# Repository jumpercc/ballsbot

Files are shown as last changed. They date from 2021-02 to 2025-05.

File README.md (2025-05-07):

# Miniature self driving car

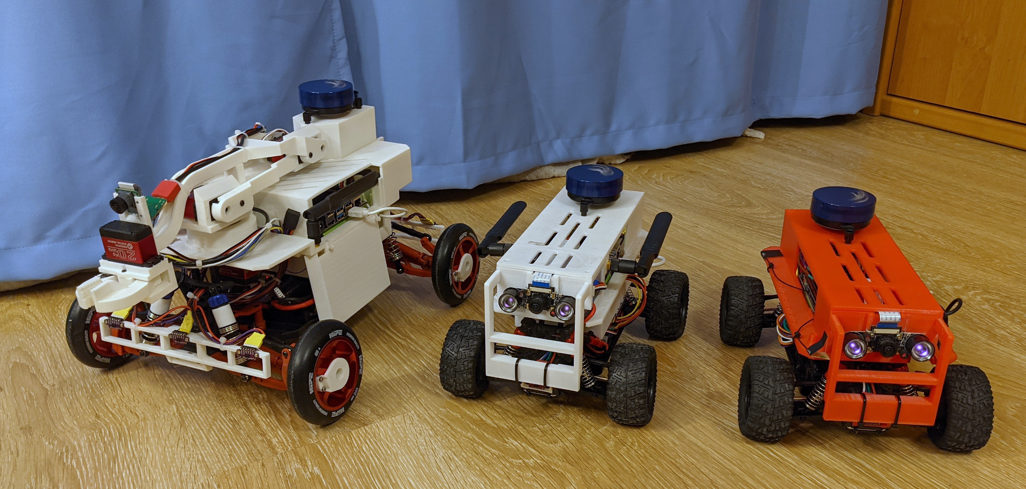
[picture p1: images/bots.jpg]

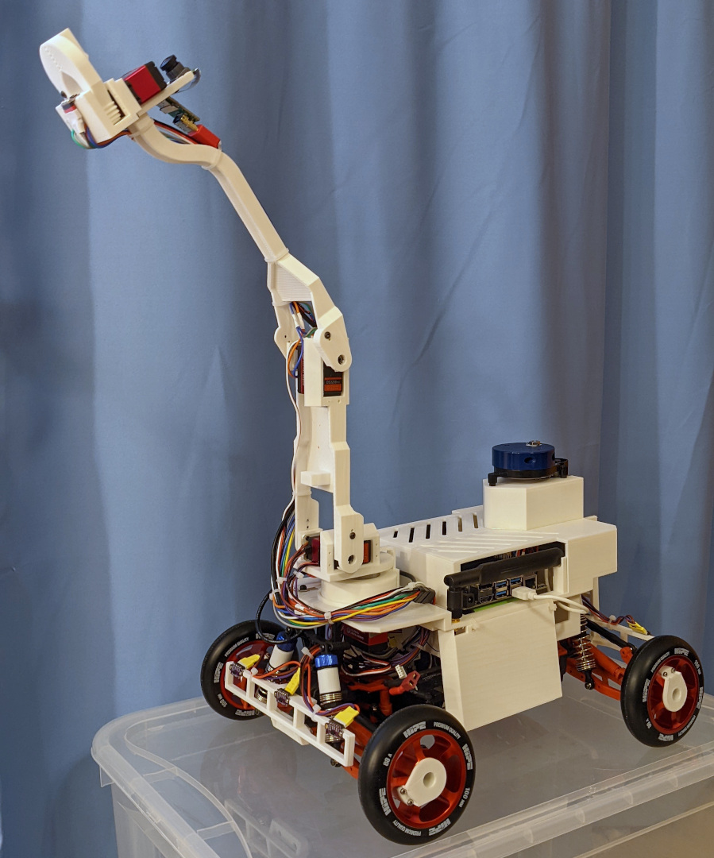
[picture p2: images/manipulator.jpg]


[A video how to construct this car](https://www.youtube.com/watch?v=rkNG0EHzA00&list=PLYvKlIOUsVXJjlYiZFUibLezPqPUq2qsj&index=1) (russian, 1/16 (small) version)

[Android app for teleoperation](https://github.com/jumpercc/ballsbot-teleoperation-android)

## Requirements

### Hardware: common for 1/16 and 1/10 models

- Nvidia Jetson Nano Developer Kit [aliexpress](https://www.aliexpress.com/item/4000765500472.html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)
- 64 GB micro sd card
- inner (not usb!) wi-fi card like [that one](https://www.aliexpress.com/item/4000144144831.html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) and IPEX Connector antennas for it
- T208 (1/16 preferred, 1/10 required) or T200 18650 UPS HAT Shield for NVIDIA Jetson Nano Developer Kit [aliexpress](https://www.aliexpress.com/item/4001332826343.html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,searchweb201602_,searchweb201603_)
- 6 (for T208) or 4 (for T200) 18650 Lithium Rechargeable Battery [aliexpress](https://www.aliexpress.com/item/32807032859.html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)
- YDLIDAR X2L or similar [aliexpress](https://www.aliexpress.com/item/4000018415971.html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)
- 9-DOF IMU BNO055 [aliexpress](https://www.aliexpress.com/item/32805406886.html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)
- PCA9685 16 Channel 12-bit PWM Servo motor Driver I2C [aliexpress](https://www.aliexpress.com/item/4000468996665.html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)
- short USB - USB-C data cable like [this one](https://www.aliexpress.com/item/32771873030.html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)
- access to 3D printer
- cables, screws, etc
- tools

### Hardware: 1/16 specific

- Remo Hobby Smax 1:16 RH1635
- SURPASS HOBBY KK 35A ESC Waterproof Electric Speed Controller for 1/16 RC Car Brushless Motor Power system [aliexpress](https://www.aliexpress.com/item/4000004474965.html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)
- Two KY-003 hall sensor module for Arduino [aliexpress](https://www.aliexpress.com/item/32907115789.html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)
- neodymium magnet about 20x3x2 mm size
- IMX219 Camera 8MP Infrared Night Vision 160 Degree FOV + 2 Infrared LED Lights [aliexpress](https://www.aliexpress.com/item/4000215557127.html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)
- 4 Channel IIC I2C Logic Level Converter Bi-Directional Module 5V to 3.3V [aliexpress](https://www.aliexpress.com/item/32771873030.html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)
- two laser distance sensors VL53L0X (6 pin) [aliexpress](https://www.aliexpress.com/item/32842745623.html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)
- additional camera, servos and others for manipulator

### Hardware: 1/10 with manipulator specific

- Remo Hobby Mmax 1:10 RH1035
- 2x Raspberry Pi Camera V2 [aliexpress](https://www.aliexpress.com/item/32846859601.html?spm=a2g0s.9042311.0.0.27424c4dI1W4Uq)
- 2x IMX219 camera sensors [aliexpress](https://www.aliexpress.com/item/4000273558224.html?spm=a2g0s.9042311.0.0.27424c4dI1W4Uq)
- 2x longer CSI cables
- engine (preferred) [aliexpress](https://www.aliexpress.com/item/4000957170077.html?spm=a2g0s.9042311.0.0.27424c4dI1W4Uq)
  - HobbyWing QuicRun 3650 Sensored Brushless G2 (25.5T)
  - QuicRun 10BL60
  - programming card
  - 3s accumulator (like Sunpadow Li-Po 3S1P 5200mAh) [market](https://market.yandex.ru/search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)
- 5x strong servos (I have 3x 30kg and 2x 20kg) [aliexpress](https://www.aliexpress.com/item/1943129663.html?spm=a2g0s.9042311.0.0.27424c4dI1W4Uq)
- 4x AS5600 magnetic encoders [aliexpress](https://www.aliexpress.com/item/4000507199893.html?spm=a2g0s.9042311.0.0.27424c4dI1W4Uq)
- 4x scooter wheels (like HIPE 5spoke 100 mm) [market](https://market.yandex.ru/catalog--aksessuary-i-zapchasti/18071952/list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)
- 1 meter thin hdmi cable
- Arducam CSI to HDMI Cable Extension Module (pack of 2) [arducam](https://www.arducam.com/product/arducam-csi-hdmi-cable-extension-module-15pin-60mm-fpc-cable-raspberry-pi-camera-specific-pack-2-1-set/)
- LTE, GPS (FIXME: haven't tested yet)
  - HUAWEI ME906e with antennas [aliexpress](https://www.aliexpress.com/item/1850815686.html?spm=a2g0s.9042311.0.0.27424c4dI1W4Uq)
  - NGFF M.2 Key B to USB 3.0 Adapter Expansion Card [aliexpress](https://www.aliexpress.com/item/4001209010055.html?spm=a2g0s.9042311.0.0.27424c4dI1W4Uq)
  - usb cable [aliexpress](https://www.aliexpress.com/item/4001289900478.html?spm=a2g0s.9042311.0.0.27424c4dI1W4Uq)
- 7x laser distance sensors VL53L0X [aliexpress](https://www.aliexpress.com/item/32842745623.html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)
- TCA9548 I2C 8-way multi-channel Expansion Board [aliexpress](https://www.aliexpress.com/item/4000067621113.html?spm=a2g0s.9042311.0.0.27424c4dPYaIDF)

### Software

- JetPack 4.6 [configuration steps](./configuration.txt)
- code from this repo
- ROS
- [Jupyter](https://jupyter.org/install) (```pip3 install notebook```)
- [YDLidar-ros](https://github.com/YDLIDAR/ydlidar_ros) for lidar (use [pdf](https://www.ydlidar.com/Public/upload/files/2020-04-13/YDLIDAR-X2-USER%20Manual.pdf) too) and install tf ros package
- ```pip3 install adafruit-pca9685``` for PCA9685
- [RTIMULib](https://github.com/jetsonhacks/RTIMULib/tree/master/Linux/python) for IMU and you need this fix (for i2c bus 0, except AS5600 magnetic encoder via TCA9548):
```
$ git diff
diff --git a/RTIMULib/RTIMUSettings.cpp b/RTIMULib/RTIMUSettings.cpp
index 783dbff..9c0333e 100644
--- a/RTIMULib/RTIMUSettings.cpp
+++ b/RTIMULib/RTIMUSettings.cpp
@@ -470,7 +470,7 @@ void RTIMUSettings::setDefaults()
     m_imuType = RTIMU_TYPE_AUTODISCOVER;
     m_I2CSlaveAddress = 0;
     m_busIsI2C = true;
-    m_I2CBus = 1;
+    m_I2CBus = 0;
     m_SPIBus = 0;
     m_SPISelect = 0;
     m_SPISpeed = 500000;
```

### SD card image

You can download SD card images from [here](https://disk.yandex.ru/d/XgYrkfBPJS2h5Q?w=1).
Install bare JetPack 4.6 first to upgrade jetson firmware.
Images are for 64GB SD cards.
```gunzip -c ballsbot-sd-2021-02-11.tgz | sudo dd of=/dev/sdb```

Login& password: `ballsbot`.

You need to connect to your wi-fi and make this connection "avaliable for all users" (checkbox in network settings).

### Dev docker

```
docker build -t ballsbot -f docker/Dockerfile .
docker run -d -v `pwd`:/home/ballsbot/projects/ballsbot -p 127.0.0.1:8080:8080 ballsbot
docker exec -it HASH-HERE bash

rm /home/ballsbot/catkin_ws/src/ballsbot_detection
source /opt/ros/melodic/setup.bash && cd /home/ballsbot/catkin_ws/ && catkin_make && source devel/setup.bash

apt-get update
/home/ballsbot/projects/ballsbot/scripts/make-ros-modules.sh  # ok if fails due to invalid arch

/home/ballsbot/projects/ballsbot/scripts/run-jupyter.sh --allow-root --port=8080 --ip=`ifconfig | grep -F 'inet ' | grep -vF 127.0.0.1 | awk '{print $2}'`
```

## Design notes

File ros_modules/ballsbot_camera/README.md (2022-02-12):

# Детектор объектов в камере, модуль для ROS

- берёт данные с камеры (csi, gstreamer)
- распознаёт объекты через SSD MobileNet
- публикует результаты

Ввиду нетривиальности сборки TensorRT кода, собрал его в отдельную библиотеку и положил рядом.
Вот исходники для [libuffssd.so](https://github.com/jumpercc/TensorRT/blob/release/8.0-jetson-nano-crosscompile-ssd/samples/sampleUffSSD/sampleUffSSD.cpp)

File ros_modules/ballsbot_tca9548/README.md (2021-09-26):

# ROS модуль для TCA9548

Переключатеть между группами из i2c устройств.

Можно читать данные с датчиков, i2c адреса которых конфликтуют.

Поддерживается до восьми устройств с одним адресом на одной TCA9548.

А, ввиду возможности задания адреса самой TCA9548, до 64ёх на одной i2c шине (через 8 TCA9548).

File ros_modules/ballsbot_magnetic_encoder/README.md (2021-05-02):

# Jetson I2C driver for rotary magnetic encoder (ROS node)

Inspired by [Arduino library](https://github.com/sosandroid/AMS_AS5048B).

Supported
- AS5048B
- AS5600

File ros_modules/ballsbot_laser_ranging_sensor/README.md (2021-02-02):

# ROS модуль для лазерного сенсора расстояния VL53L0X

Собрал на основе [jetsonhacks/JHVL53L0X](https://github.com/jetsonhacks/JHVL53L0X)

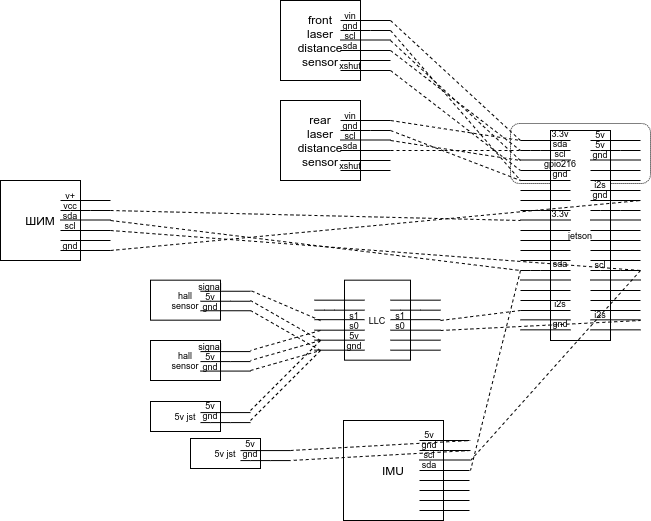
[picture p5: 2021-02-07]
images/ballsbot t208.png

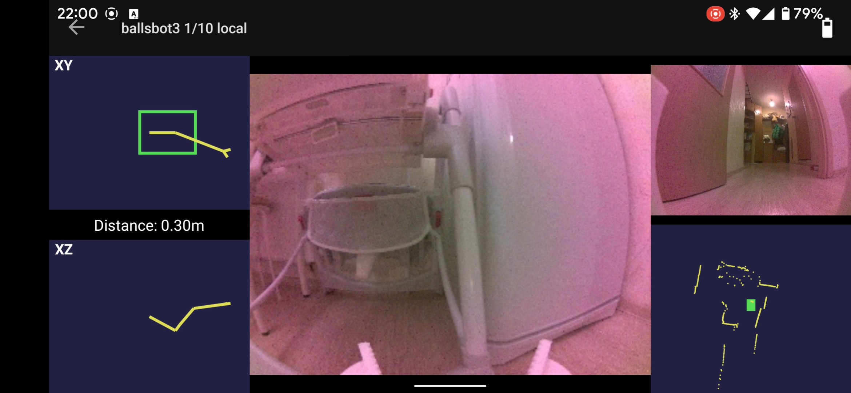
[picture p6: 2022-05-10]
images/teleoperation-app.jpg

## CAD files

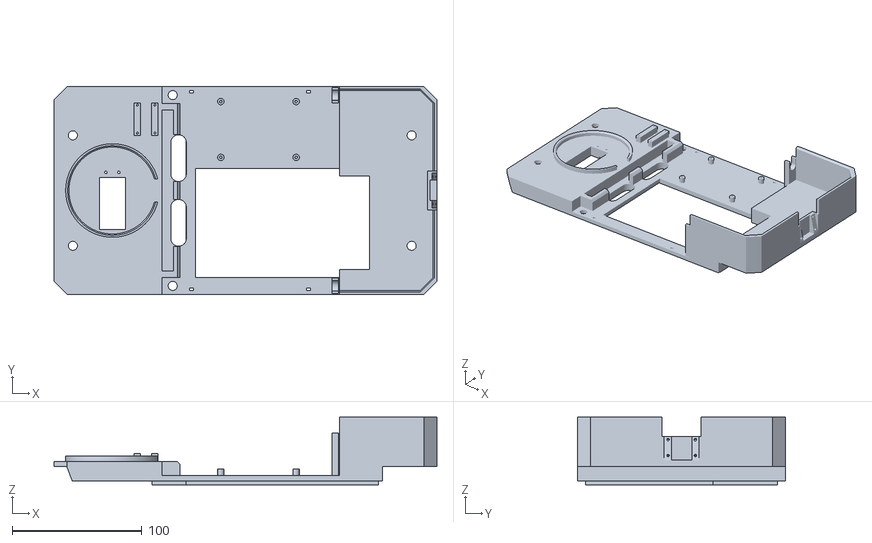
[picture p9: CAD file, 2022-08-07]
stl/1-10/one-ten-main-plate.stl
295.0 x 160.0 x 52.0

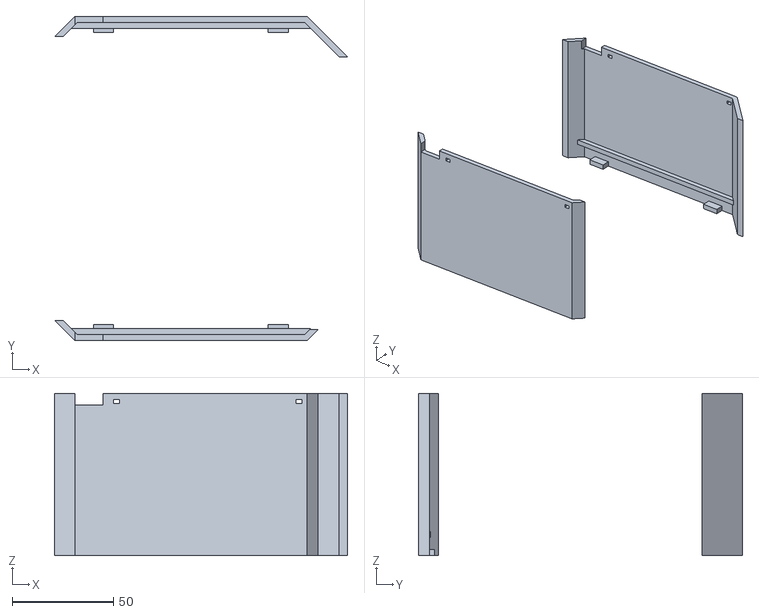
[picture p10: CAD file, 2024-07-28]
stl/1-10/one-ten-side-covers.stl
144.5 x 160.0 x 80.0

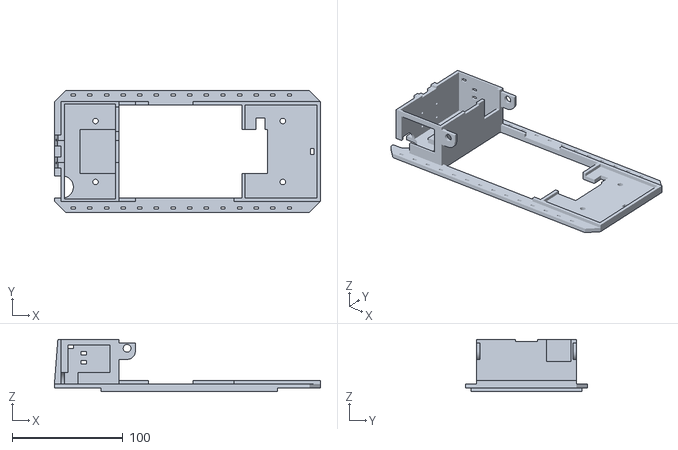
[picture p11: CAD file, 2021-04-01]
stl/1-16/car-bottom.stl
240.0 x 110.0 x 47.0

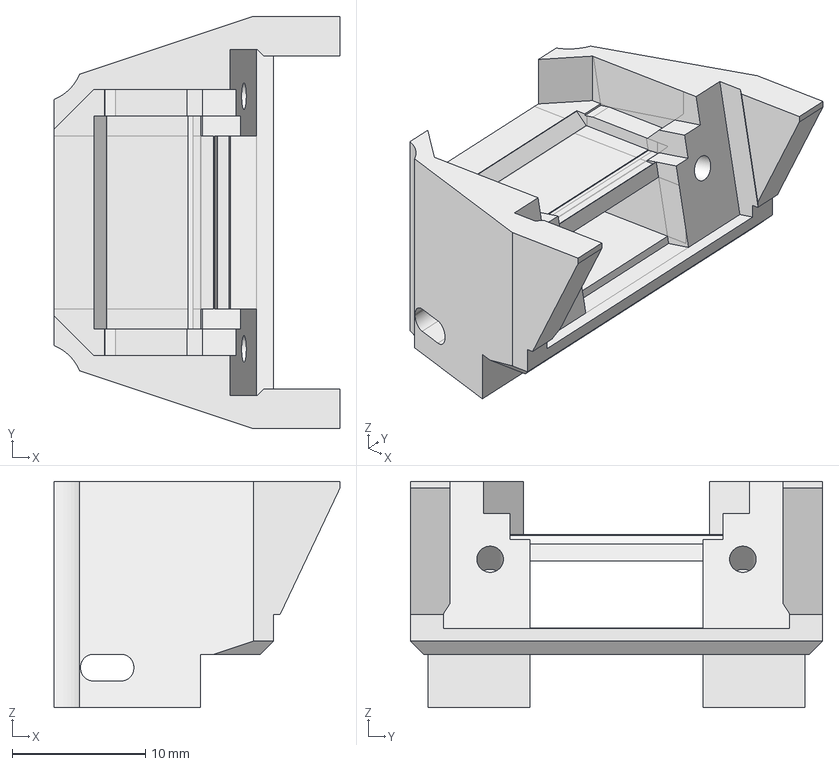
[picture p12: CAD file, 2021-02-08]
stl/1-16/laser-sensor/laser-sensor-base.FCStd
21.5 x 31.0 x 17.0 mm

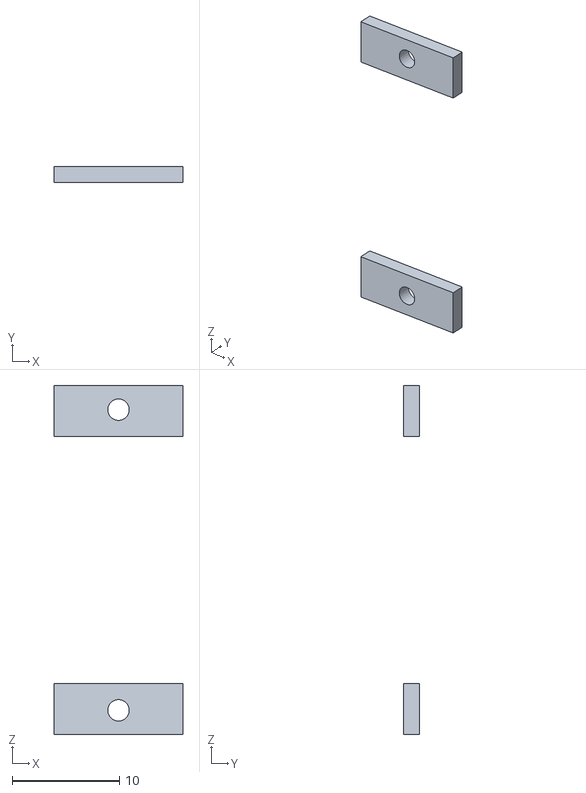
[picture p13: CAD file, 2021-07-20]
stl/1-16/manipulator/small-servo-adapter.stl
12.0 x 1.50 x 32.5

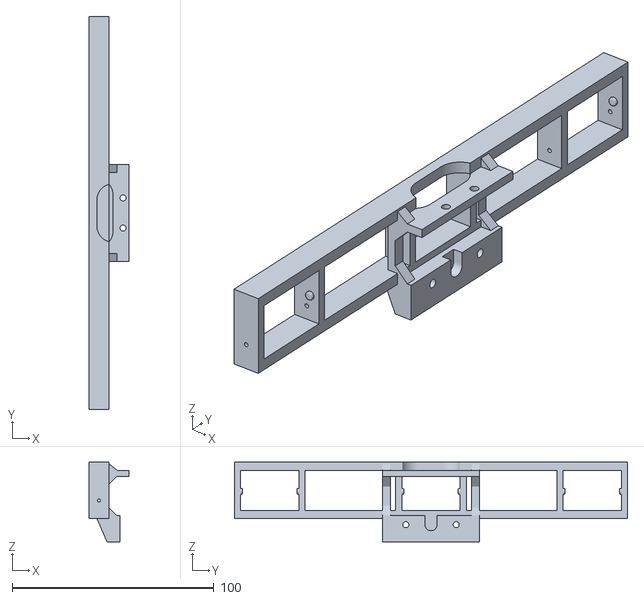
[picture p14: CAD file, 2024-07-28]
stl/1-10/one-ten-front-bumper.stl
20.0 x 195.0 x 39.5

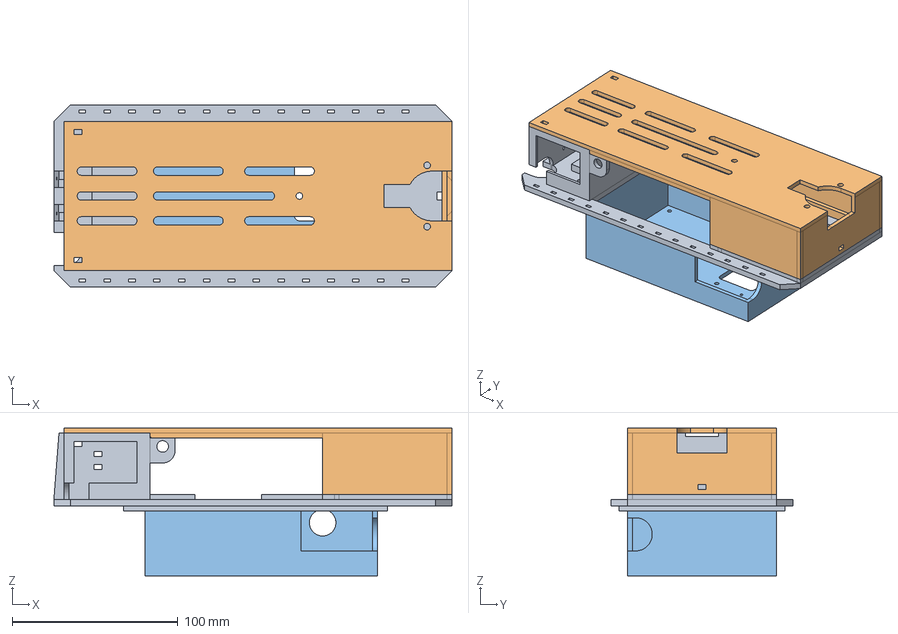
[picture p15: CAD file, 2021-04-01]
stl/1-16/car-body.FCStd
240.0 x 110.0 x 89.0 mm
bottom t20X
roof t20X
jetson basket t208.

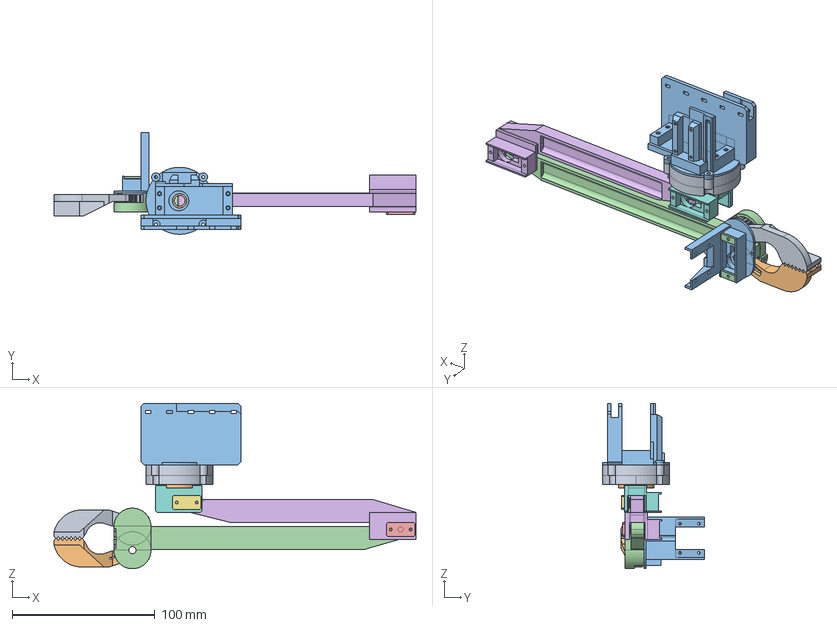
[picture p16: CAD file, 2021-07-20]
stl/1-16/manipulator/manipulator.FCStd
253.8 x 71.2 x 116.0 mm
h3-left-claw
h3-right-claw
h3-claw-top
h2-manipulator001
h2-pin
h1-to-h2
h1-pin
h1-servo001
h0-outer-ring
h0-inner
h0-car-attachment003
small-servo-adapter

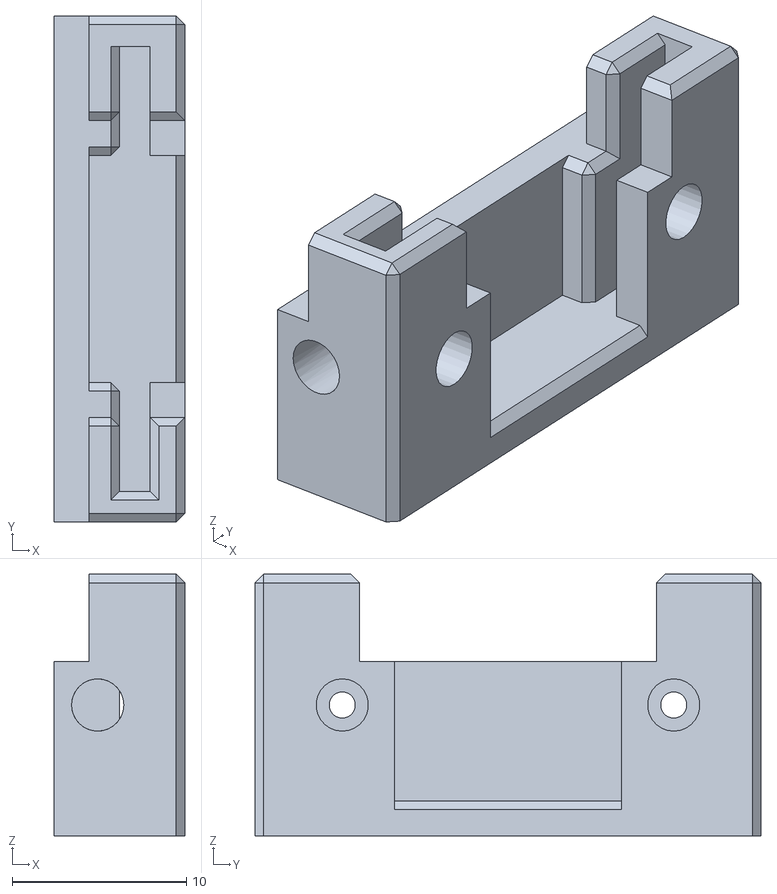
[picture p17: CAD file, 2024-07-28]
stl/1-10/distance-sensor-holder.stl
7.50 x 29.0 x 15.0

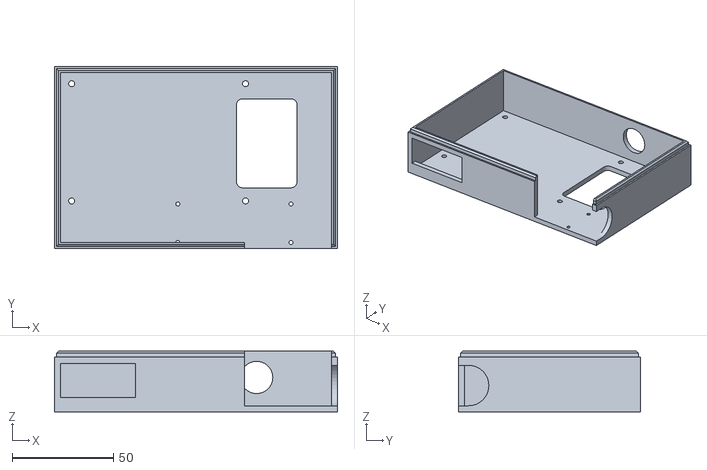
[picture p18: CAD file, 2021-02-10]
stl/1-16/car-jetson-basket-t200.stl
140.0 x 90.0 x 30.0

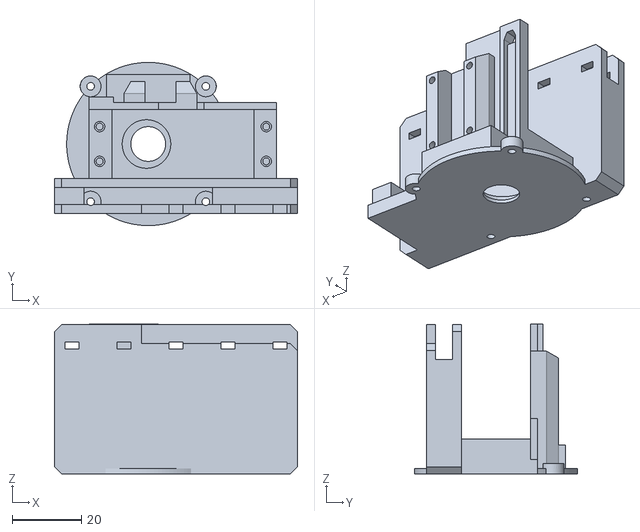
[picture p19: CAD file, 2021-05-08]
stl/1-16/manipulator/h0-car-attachment.stl
70.0 x 47.0 x 43.1

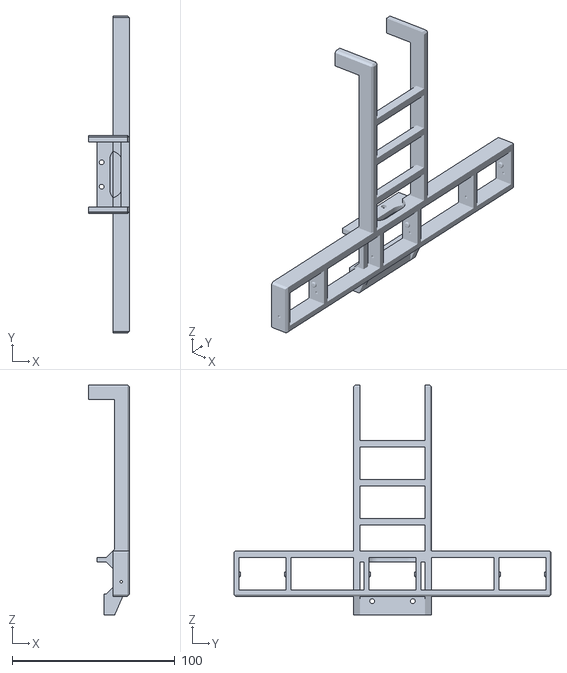
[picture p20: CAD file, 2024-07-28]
stl/1-10/one-ten-rear-bumper.stl
25.0 x 195.0 x 141.5

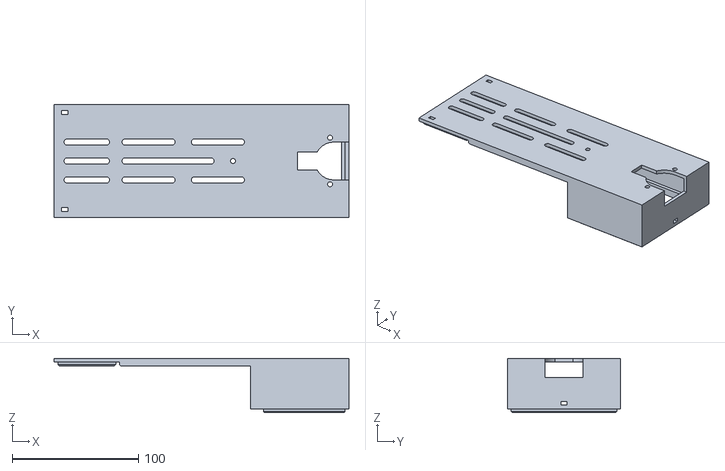
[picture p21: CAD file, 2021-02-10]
stl/1-16/car-top.stl
234.0 x 90.0 x 43.0

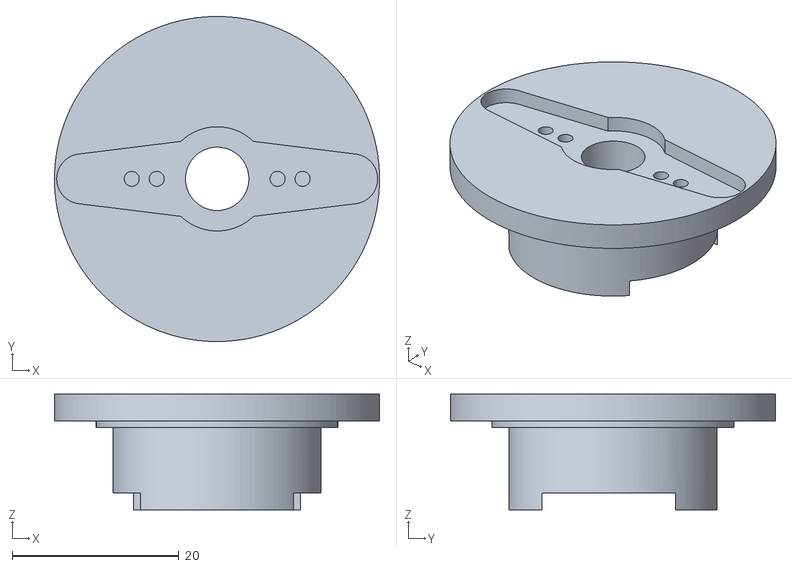
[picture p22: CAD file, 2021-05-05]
stl/1-16/manipulator/h0-inner.stl
39.0 x 39.0 x 13.9

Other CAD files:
stl/1-10/car-parts.FCStd
stl/1-16/car-jetson-basket-t208.stl
stl/1-16/manipulator/h2-manipulator.stl
stl/1-10/one-ten-amortization-hardener.stl
stl/1-10/car-hall-sensors-shelf.FCStd
stl/1-10/flexible-claw-p-claw-left-hard.stl
stl/1-10/flexible-claw-p-claw-left-soft.stl
stl/1-10/flexible-claw-p-claw-right-hard.stl
stl/1-10/flexible-claw-p-claw-right-soft.stl
stl/1-10/flexible-claw.FCStd
stl/1-10/one-ten-claw-bottom.stl
stl/1-10/one-ten-claw-magnet-holder.stl
stl/1-10/one-ten-gsm-adapter.stl
stl/1-10/one-ten-hall-sensors-shelf.stl
stl/1-10/one-ten-jetson-basket.stl
stl/1-10/one-ten-left-claw.stl
stl/1-10/one-ten-lidar-box.stl
stl/1-10/one-ten-m0-bottom.stl
stl/1-10/one-ten-m0-cup.stl
stl/1-10/one-ten-m0-inner-part.stl
stl/1-10/one-ten-m0-magnet-hoder.stl
stl/1-10/one-ten-m1.stl
stl/1-10/one-ten-m2.stl
stl/1-10/one-ten-magnetic-holder-pin.stl
stl/1-10/one-ten-right-claw.stl
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

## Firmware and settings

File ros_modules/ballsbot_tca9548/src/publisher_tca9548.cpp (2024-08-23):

#include <stdint.h>
#include <cstdlib>
#include <iostream>
#include <vector>
#include <string>
#include <memory>
#include <future>
#include <thread>
#include <chrono>
#include <unordered_map>
#include "ros/ros.h"
#include "ballsbot_tca9548/LaserDistance.h"
#include "ballsbot_tca9548/EncoderAngle.h"
#include "tca9548.h"
#include "VL53L0X.h"
#include "magnetic_encoder_driver.h"
using namespace std::chrono_literals;

const uint16_t kNotAvailable = 0xFFFFu;

enum kDeviceType {
    kLaserRangingSensor = 0,
    kMagneticEncoderAS5600 = 1,
    kMagneticEncoderAS5048B = 2,
};

struct I2CDevice {
    kDeviceType device_type_;
    std::string device_name_;
};

struct ConfigItem {
    uint8_t state_bits;
    std::vector<I2CDevice> devices;
};

std::shared_ptr<VL53L0X> GetLaserSensor(uint8_t bus_number) {
    auto sensor = std::make_shared<VL53L0X>(bus_number, 0x29);
    if (!sensor->openVL53L0X()) {
        ROS_INFO("Unable to open VL53L0X");
        exit(-1);
    }
    sensor->init();
    sensor->setTimeout(500);
#if defined LONG_RANGE
    // lower the return signal rate limit (default is 0.25 MCPS)
    sensor->setSignalRateLimit(0.1);
    // increase laser pulse periods (defaults are 14 and 10 PCLKs)
    sensor->setVcselPulsePeriod(VL53L0X::VcselPeriodPreRange, 18);
    sensor->setVcselPulsePeriod(VL53L0X::VcselPeriodFinalRange, 14);
#endif

#if defined HIGH_SPEED
    // reduce timing budget to 20 ms (default is about 33 ms)
    sensor->setMeasurementTimingBudget(20000);
#elif defined HIGH_ACCURACY
    // increase timing budget to 200 ms
    sensor->setMeasurementTimingBudget(200000);
#endif
    return sensor;
}

std::shared_ptr<EncoderBase> GetEncoder(uint8_t bus_number, kDeviceType device_type) {
    std::shared_ptr<EncoderBase> result;
    if (device_type == kMagneticEncoderAS5600) {
        result = std::make_shared<AMS_AS5600>(bus_number);
    } else {
        result = std::make_shared<AMS_AS5048B>(bus_number);
    }
    result->OpenSensor();
    result->SetClockWise(false);  // TODO from config
    return result;
}

size_t CountDevices(const std::vector<ConfigItem>& config, kDeviceType device_type) {
    size_t result = 0;
    for (auto lane : config) {
        for (auto device : lane.devices) {
            if (device.device_type_ == device_type) {
                result += 1;
            }
        }
    }
    return result;
}

std::unordered_map<uint8_t, std::shared_ptr<VL53L0X>> laser_sensors_cache;

uint16_t GetDistanceFromLaserSensor(uint8_t bus_number, uint8_t sensor_key) {
    if (laser_sensors_cache.find(sensor_key) == laser_sensors_cache.end()) {
        laser_sensors_cache[sensor_key] = GetLaserSensor(bus_number);
    }
    auto laser_sensor = laser_sensors_cache[sensor_key];
    uint16_t distance = laser_sensor->readRangeSingleMillimeters();
    if (laser_sensor->timeoutOccurred()) {
        ROS_INFO("Sensor timeout!");
        laser_sensor->closeVL53L0X();
        laser_sensors_cache.erase(laser_sensors_cache.find(sensor_key));
        return kNotAvailable;
    } else if (distance > 2500) {
        distance = 2500;
    }
    return distance;
}

size_t timeouts_count = 0;

uint16_t GetDistanceFromLaserSensorWithTimeout(uint8_t bus_number, uint8_t sensor_key) {
    std::packaged_task<uint16_t(uint8_t, uint8_t)> task(GetDistanceFromLaserSensor);
    auto future = task.get_future();
    std::thread thr(std::move(task), bus_number, sensor_key);
    if (future.wait_for(1s) != std::future_status::timeout) {
        thr.join();
        return future.get();
    } else {
        thr.detach();
        ROS_INFO("Sensor timeout, thread still running!");
        if (++timeouts_count > 5) {
            throw std::runtime_error("timeouts limit exceeded for " + std::to_string(sensor_key));
        }
        auto laser_sensor = laser_sensors_cache[sensor_key];
        if (laser_sensor) {
            laser_sensor->closeVL53L0X();
        }
        laser_sensors_cache.erase(laser_sensors_cache.find(sensor_key));
        return kNotAvailable;
    }
}

std::unordered_map<uint8_t, std::shared_ptr<EncoderBase>> encoders_cache;

double GetAngleFromMagneticEncoder(uint8_t bus_number, kDeviceType device_type,
                                   uint8_t sensor_key) {
    if (encoders_cache.find(sensor_key) == encoders_cache.end()) {
        encoders_cache[sensor_key] = GetEncoder(bus_number, device_type);
    }
    auto encoder = encoders_cache[sensor_key];
    double angle = encoder->GetAngle(U_RAD, true);
    return angle;
}

int main(int argc, char* argv[]) {
    if (argc < 3) {
        std::cerr << "USAGE: publisher_tca9548 <bus_number> <device_address>\n";
        exit(1);
    }
    uint8_t bus_number = atoi(argv[1]);
    uint8_t address = atoi(argv[2]);

    std::vector<ConfigItem> config = {  // TODO config to external text file
        {0b00000001u, {{kLaserRangingSensor, "rear-right"}}},
        {0b00000010u, {{kLaserRangingSensor, "rear-left"}}},
        {0b00000100u, {{kLaserRangingSensor, "front-left"}}},
        {0b00001000u, {{kLaserRangingSensor, "front-right"}}},
        {0b00010000u, {{kMagneticEncoderAS5600, "m-2"}}},
        {0b00100000u,
         {
             {kLaserRangingSensor, "manipulator"},
             {kMagneticEncoderAS5600, "m-claw"},
         }},
        {0b01000000u,
         {
             {kLaserRangingSensor, "front-center"},
             {kMagneticEncoderAS5600, "m-0"},
         }},
        {0b10000000u,
         {
             {kLaserRangingSensor, "rear-center"},
             {kMagneticEncoderAS5600, "m-1"},
         }},
    };

    ros::init(argc, argv, "ballsbot_tca9548");
    ros::NodeHandle n;

    TCA9548 controller(bus_number, address);
    controller.Start();

    ballsbot_tca9548::LaserDistance ld_msg;
    uint16_t distance;
    auto laser_distance_publisher = n.advertise<ballsbot_tca9548::LaserDistance>(
        "laser_distance", CountDevices(config, kLaserRangingSensor) || 1);

    ballsbot_tca9548::EncoderAngle enc_msg;
    double angle;
    auto magnetic_encoder_publisher = n.advertise<ballsbot_tca9548::EncoderAngle>(
        "magnetic_encoder", CountDevices(config, kMagneticEncoderAS5600) || 1);

    ros::Rate loop_rate(4);
    while (ros::ok()) {
        for (auto config_item : config) {
            controller.SetState(config_item.state_bits);
            for (auto device : config_item.devices) {
                if (device.device_type_ == kLaserRangingSensor) {
                    distance =
                        GetDistanceFromLaserSensorWithTimeout(bus_number, config_item.state_bits);
                    if (distance == kNotAvailable) {
                        continue;
                    }
                    ld_msg.distance_in_mm = distance;
                    ld_msg.sensor_name = device.device_name_;
                    ld_msg.header.stamp = ros::Time::now();
                    // ROS_INFO("%s: %i mm", ld_msg.sensor_name.c_str(), ld_msg.distance_in_mm);
                    laser_distance_publisher.publish(ld_msg);
                } else if (device.device_type_ == kMagneticEncoderAS5600 ||
                           device.device_type_ == kMagneticEncoderAS5048B) {
                    angle = GetAngleFromMagneticEncoder(bus_number, device.device_type_,
                                                        config_item.state_bits);
                    enc_msg.angle = angle;
                    enc_msg.sensor_name = device.device_name_;
                    enc_msg.header.stamp = ros::Time::now();
                    // ROS_INFO("%s: %0.4f rad", enc_msg.encoder_name.c_str(), enc_msg.angle);
                    magnetic_encoder_publisher.publish(enc_msg);
                }
            }
        }
        ros::spinOnce();
        loop_rate.sleep();
    }

    controller.SetState(0);
    controller.Finish();
    return 0;
}

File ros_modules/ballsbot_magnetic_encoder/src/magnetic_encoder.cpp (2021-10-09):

#include "magnetic_encoder_driver.h"
#include "ros/ros.h"
#include "ballsbot_magnetic_encoder/EncoderAngle.h"
#include <string>
#include <sstream>

int main(int argc, char **argv) {
    unsigned char bus = 0;
    std::string encoder_name("default");
    std::string topic_name("magnetic_encoder");

    if (argc >= 2) {
        bus = atoi(argv[1]);
    }

    ros::init(argc, argv, "ballsbot_magnetic_encoder");

    ros::NodeHandle n;
    ros::Publisher chatter_pub =
        n.advertise<ballsbot_magnetic_encoder::EncoderAngle>(topic_name, 1);
    ros::Rate loop_rate(10);

    AMS_AS5600 a_sensor(bus);
    a_sensor.OpenSensor();
    a_sensor.SetClockWise(false);

    while (ros::ok()) {
        ballsbot_magnetic_encoder::EncoderAngle msg;

        msg.angle = a_sensor.GetAngle(U_RAD, true);
        msg.encoder_name = encoder_name;

        ROS_INFO("%s: %0.4f", msg.encoder_name.c_str(), msg.angle);

        chatter_pub.publish(msg);
        ros::spinOnce();
        loop_rate.sleep();
    }

    a_sensor.CloseSensor();
}

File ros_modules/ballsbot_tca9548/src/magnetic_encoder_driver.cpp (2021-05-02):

#include <math.h>
#include <stdio.h>
#include <fcntl.h>
#include <linux/i2c-dev.h>
#include <sys/ioctl.h>
#include <unistd.h>
#include <cstring>
#include <cerrno>
extern "C" {
#include <i2c/smbus.h>
}
#include <stdexcept>
#include "magnetic_encoder_driver.h"

EncoderConstants GetAS5048BConstants() {
    EncoderConstants result = {0x40, 0xFE, 16384.0, 0b11111111111111};
    return result;
}

EncoderConstants GetAS5600Constants() {
    EncoderConstants result = {0x36, 0x0E, 4096.0, 0b111111111111};
    return result;
}

void EncoderBase::OpenSensor() {
    clock_wise_ = false;
    last_angle_raw_ = 0.0;

    char file_name_buffer[32];
    sprintf(file_name_buffer, "/dev/i2c-%d", i2c_bus_number_);
    i2c_file_descriptor_ = open(file_name_buffer, O_RDWR);
    if (i2c_file_descriptor_ < 0) {
        throw std::runtime_error(std::string("Could not open the file /dev/i2c-xxx: ") +
                                 std::strerror(errno));
    }
    if (ioctl(i2c_file_descriptor_, I2C_SLAVE, constants_.i2c_address) < 0) {
        throw std::runtime_error(std::string("Could not open the device on the bus: ") +
                                 std::strerror(errno));
    }
}

void EncoderBase::CloseSensor() {
    if (i2c_file_descriptor_ > 0) {
        int close_return_value = close(i2c_file_descriptor_);
        i2c_file_descriptor_ = -1;
        if (close_return_value != 0) {
            throw std::runtime_error(std::string("close failed: ") + std::strerror(errno));
        }
    }
}

void EncoderBase::SetClockWise(bool cw) {
    clock_wise_ = cw;
    last_angle_raw_ = 0.0;
}

double EncoderBase::GetAngle(int unit, bool new_val) {
    double angle_raw;

    if (new_val) {
        if (clock_wise_) {
            angle_raw = static_cast<double>(constants_.inverse_bits -
                                            ReadAngle(constants_.register_address));
        } else {
            angle_raw = static_cast<double>(ReadAngle(constants_.register_address));
        }
        last_angle_raw_ = angle_raw;
    } else {
        angle_raw = last_angle_raw_;
    }

    return ConvertAngle(unit, angle_raw);
}

double EncoderBase::ConvertAngle(int unit, double angle) {
    // convert raw sensor reading into angle unit

    double result;

    switch (unit) {
        case U_RAW:
            // Sensor raw measurement
            result = angle;
            break;
        case U_TRN:
            // full turn ratio
            result = (angle / constants_.resolution);
            break;
        case U_DEG:
            // degree
            result = (angle / constants_.resolution) * 360.0;
            break;
        case U_RAD:
            // Radian
            result = (angle / constants_.resolution) * 2 * M_PI;
            break;
    }
    return result;
}

uint16_t AMS_AS5048B::ReadAngle(uint8_t address) {
    // 16 bit value got from 2 8bits registers (7..0 MSB + 5..0 LSB) => 14 bits value
    uint16_t result = i2c_smbus_read_word_data(i2c_file_descriptor_, address);
    result = (result & 0xFF) << 6 | (result & 0x3F00) >> 8;
    return result;
}

uint16_t AMS_AS5600::ReadAngle(uint8_t address) {
    // 16 bit value got from 2 8bits registers (7..0 MSB + 3..0 LSB) => 12 bits value
    uint16_t result = i2c_smbus_read_word_data(i2c_file_descriptor_, address);
    result = (result & 0xFF000) >> 8 | (result & 0x0F) << 8;
    return result;
}

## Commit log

2020-05-17 lidar and cameras
2020-06-17 lidar fix
2020-06-17 csi camera
2020-06-17 servos fix
2020-06-20 raw odometry
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2020-08-09 right odometry + bug fixes
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2020-08-10 draw lidar clouds history
2020-08-21 odometry fixes
2020-08-24 odometry fix with walls (beta)
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2020-10-25 3p car parts
    [car-body.FCStd, car-buffer.FCStd, car-hall-sensors-shelf.FCStd]
2020-11-02 stls generated
    [car-bottom.stl, car-buffer.stl, car-hall-sensors-shelf.FCStd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]
2020-11-04 stl: antennas, added
    [car-body.FCStd, car-bottom.stl]
2020-11-13 filament economy
    [car-body.FCStd, car-bottom.stl]
2020-11-18 T208 ups hat support
    [car-body.FCStd, car-bottom-t200.stl, car-bottom-t208.stl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]
2020-11-18 monor stl fixes
    [car-body.FCStd]
2020-11-19 stl fixes
    [car-body.FCStd, car-bottom-t208.stl, car-jetson-basket-t208.stl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]
2020-11-23 notebooks for camera and CameraDetector
2020-11-25 new tiny 3d printed parts
    [car-amortizarion-fix.FCStd, car-amortization-fix.stl]
2021-01-03 car-amortizarion-fix fixed
    [car-amortizarion-fix.FCStd, car-amortization-fix.stl]
2021-01-05 stl, t208 jst hole added
    [car-body.FCStd, car-jetson-basket-t208.stl]
2021-01-06 fixes + lidar launch file
2021-01-06 amort fix fixed
    [car-amortizarion-fix.FCStd, car-amortization-fix.stl]
2021-01-06 servos, alternative bus number
2021-01-06 stl: jetson basket driver holes fixed
    [car-body.FCStd, car-jetson-basket-t208.stl]
2021-01-06 stl: hall sensors shelf length reduced
    [car-hall-sensors-shelf.FCStd, car-hall-sensors-shelf.stl]
2021-01-07 imu error fixed (due to update some libs)
2021-01-07 notebooks for testing imu, and hall sensors
2021-01-08 t208 alternative odometry pin
2021-01-09 stl: body parts connection fixed
    [car-body.FCStd, car-jetson-basket-t208.stl]
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2021-01-14 useless constant removed
    [car-body.FCStd, car-bottom-t208.stl]
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2021-02-02 VL53L0X ranging laser sensor ROS module
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2021-02-08 laser sensors stl and integration
    [laser-sensor-base.FCStd, laser-sensor-base.stl]
2021-02-10 stl unification
    [car-body.FCStd, car-bottom-t200.stl, car-bottom-t208.stl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]
2021-02-18 manipulator draft
    [manipulator.FCStd]
2021-02-24 dummy manipulator
    [h0-car-attachment.stl, h0-inner.stl, h0-outer-ring.stl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]
2021-02-24 stl fix
    [h1-servo.stl, manipulator.FCStd]
2021-02-24 new manipulator
    [car-body.FCStd, h0-car-attachment.stl, h0-inner.stl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]
2021-02-25 stl, new manipulator
    [h-cable-holder.stl, h1-to-h2.stl, h2-manipulator.stl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]
2021-02-26 stl manipulator fixes
    [h-cable-holder.stl, h0-car-attachment.stl, h1-to-h2.stl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]
2021-02-28 servo tuning, dummy manipulator
2021-03-02 stl manipulator, claw added
    [h-cable-holder.stl, h0-car-attachment.stl, h2-claw-top.stl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]
2021-03-03 stl manipulator update
    [h2-left-claw.stl, h2-manipulator.stl, manipulator.FCStd]
2021-03-06 stl fixes, manipulator
    [h2-left-claw.stl, h2-right-claw.stl, manipulator.FCStd]
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2021-03-07 manipulator stl: bigger servo #0
    [h0-car-attachment.stl, h0-inner.stl, h0-outer-ring.stl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]
2021-03-07 manipulator stl: bugfixes
    [h0-car-attachment.stl, h0-outer-ring.stl, manipulator.FCStd]
2021-03-08 manipulator stl: fixes
    [h0-outer-ring.stl, manipulator.FCStd]
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2021-03-21 stl structure
    [car-body.FCStd, car-bottom.stl, h-cable-holder.stl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]
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2021-03-29 stl: new manipulator
    [h-cable-holder.stl, h0-car-attachment.stl, h1-to-h2.stl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]
2021-03-29 stl, manipulator, top plate update
    [h2-claw-top.stl, manipulator.FCStd]
2021-04-01 stl: manipulator fixes
    [h-cable-holder.stl, h2-claw-top.stl, h2-manipulator.stl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]
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2021-04-01 stl fixes for manipulator
    [car-body.FCStd, car-bottom.stl, h-camera-cable-holder.stl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]
2021-04-01 manipulator with a camera: code
2021-04-25 stl: manipilator: hdmi module
    [balancer.stl, balanser.FCStd, h0-car-attachment.stl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]
2021-05-02 balanser stl fixed
    [balancer.stl, balanser.FCStd]
2021-05-05 manipulator stl: bearings added
    [h0-car-attachment.stl, h0-inner.stl, h0-outer-ring.stl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]
2021-05-08 manipulator stl fix
    [h0-car-attachment.stl, manipulator.FCStd]
2021-05-08 manipulator servos tuned again
2021-05-10 raw_grid added to saved track
2021-06-08 draw lidar and manipulator images in anothre process
2021-06-21 1/10 car stl draft
    [car-parts.FCStd, one-ten-amortization-hardener.stl]
2021-06-22 1/10 car stl draft update
    [car-parts.FCStd]
2021-07-12 1/10 car stl
    [car-parts.FCStd, one-ten-claw-top.stl, one-ten-jetson-basket.stl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]
2021-07-14 1/10 car stl fixes
    [car-parts.FCStd, one-ten-jetson-basket.stl, one-ten-main-plate.stl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]
2021-07-23 1/10 stl: bumper
    [car-parts.FCStd, one-ten-front-buffer.stl]
2021-07-24 1/10 stl: rear bumper
    [car-parts.FCStd, one-ten-rear-bumper.stl]
2021-07-27 lidar calibration range limit to config option
2021-08-04 second camera without manipulator
2021-08-06 1/10 new servo limits
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2021-08-09 1/10 stl: new claw servo
    [car-parts.FCStd, one-ten-claw-bottom.stl, one-ten-claw-top.stl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]
2021-08-14 1/10 stl update
    [car-parts.FCStd, one-ten-m2.stl]
2021-08-16 claw stl fixed
    [car-parts.FCStd, one-ten-claw-bottom.stl, one-ten-left-claw.stl]
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2021-08-25 scooter wheel adapter
    [scooter-wheel-adapter-inner.stl, scooter-wheel-adapter-outer.stl, scooter-wheel-adapter.FCStd]
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2021-08-27 stl files reorganized
    [balancer.stl, balanser.FCStd, car-amortizarion-fix.FCStd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]
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2021-09-28 1/10 stl claw sensors
    [car-parts.FCStd, one-ten-claw-bottom.stl, one-ten-claw-magnet-holder.stl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]
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2021-10-03 better-sensor-messages steering fot 1/16 fix
2021-10-03 temporary hall sensors config
2021-10-05 explorer turn radius fix for steering scale 2
2021-10-06 1/10 stl bumpers: 3 laser sensor modules on each
    [car-parts.FCStd, one-ten-front-bumper.stl, one-ten-rear-bumper.stl]
2021-11-05 tca i2c 1->0, imu i2c 0->1 for magnetic encoder (fix address conflict)
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2021-11-07 manipulator logging for jammed state
    [publisher_ups.py]
2021-11-07 mew m0 magnit holder
    [car-parts.FCStd, one-ten-m0-magnet-hoder.stl]
2021-12-12 bugfix and configuration commands list draft
    [configuration.txt]
2022-02-12 jetpack 4.4 -> 4.6
    [configuration.txt]
2022-02-20 manipulator laser sensor distance on a dash
2022-05-10 teleoperation api
    [configuration.txt]
2022-06-21 gsm basic support
    [car-parts.FCStd, one-ten-gsm-adapter.stl]
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2022-07-03 manual car movement for claw-detector autopilot mode
2022-08-07 better main plate for 1/10
    [car-parts.FCStd, one-ten-jetson-basket.stl, one-ten-main-plate.stl]
2023-01-14 manipulator calibration
    [configuration.txt]
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2023-04-06 stl: magnet holder pin fix
    [car-parts.FCStd, one-ten-magnetic-holder-pin.stl]
2023-04-18 bugfix and calibration
2023-04-18 dev docker
    [ydlidar.urdf]
2023-04-23 dev docker fix
    [configuration.txt, ydlidar.urdf]
2023-04-26 better resolution for one camera bot
2023-05-05 more ros draft
    [configuration.txt]
2023-05-20 more-ros draft
    [ballsbot.urdf, configuration.txt]
2024-06-16 new claw
    [flexible-claw-p-claw-left-hard.stl, flexible-claw-p-claw-left-soft.stl, flexible-claw-p-claw-right-hard.stl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]
2024-07-11 1/10 claw and amortization
    [car-parts.FCStd, one-ten-amortization-hardener.stl]
2024-07-28 bumpers and side walls
    [distance-sensor-holder.stl, one-ten-front-bumper.stl, one-ten-rear-bumper.stl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]
2024-08-22 ndt pose fix bugfix
    [VL53L0X.cpp]
2024-08-23 ndt pose fix optimized
    [publisher_wheel_odometry.py]
2025-05-07 ndt-pose-fix save a progress
    [configuration.txt]
